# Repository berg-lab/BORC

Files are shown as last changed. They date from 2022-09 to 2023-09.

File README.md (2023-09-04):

# BORC
Battery-Operated Radiator Control

A low-power automatic radiator control that is designed to retrofit on steam radiators that use Honeywell's T104A1040 Zone Valve Operator
uses LowPowerLab's [DualOptiboot](https://github.com/LowPowerLab/DualOptiboot) bootloader for the ATmega1284P.

This repo contains:
- PCB design files and schematic for control board, power board and LED board for the BORC.
- Firmware for a low-power radiator control node
- Logger script to get real-time current data from the BORC

---

## Dependencies

To compile the firmware, [Arduino IDE 1.8.19](https://www.arduino.cc/en/software) or higher is required.

The firmware requires the following libraries installed:
- [RFM69](https://github.com/LowPowerLab/RFM69)
- [SPIFlash](https://github.com/LowPowerLab/SPIFlash)
- [LowPower](https://github.com/LowPowerLab/LowPower)
- [Adafruit PWM Servo Driver Library](https://github.com/adafruit/Adafruit-PWM-Servo-Driver-Library)

The firmware also requires the Moteino Board definitions installed following [this guide](https://lowpowerlab.com/guide/moteino/programming-libraries/).

---

## Logger script

The [logger script](https://github.com/berg-lab/BORC/blob/master/logger/logger.py) enables capturing current usage data over the serial port on the BORC.

### Prerequisites:
- [pip](https://pip.pypa.io/en/stable/installation/)
- [Pyserial](https://pypi.org/project/pyserial/)

### Run:
Run the script using the following command over a command line interface:

_For Windows:_
```
python logger.py -c COM15 -n filename
```

_For MacOS/Linux:_
```
python logger.py -c /dev/ttyusb0 -n filename
```

### Notes:
- Change `python` to `python3` if using Python version 3.
- Change `filename` to something referencing the test to keep the generated files organized. The current date/time is automatically added to the filename.
- The script automatically adds the `.csv` extension to the filename, so there's no need to include it in the arguments when running it.
- For Windows, go to device manager and find the COM port of the BORC under "Ports" section and replace `COM15` in the command above.
- For MacOS or Linux, use `ls /dev/tty.*` command in terminal to find the COM port of the BORC, and replace `/dev/ttyusb0` above with the full path of the COM port.
- Use `-h` command to bring a help menu (eg. `python logger.py -h`).
- If the servo doesn't move in some areas, you can adjust the default min and max limits to the particular servo installed. The default limits should be set to where the servo is guaranteed to move, and beyond these limits, the servo will not respond. Typical min limit for a 270° servo is 3600 and max limit is 3950. You can increase or decrease these limits to see where the servo being tested begins to move.
- Default baudrate for the BORC is `115200`. If updated, make sure to update the same in the logger script.

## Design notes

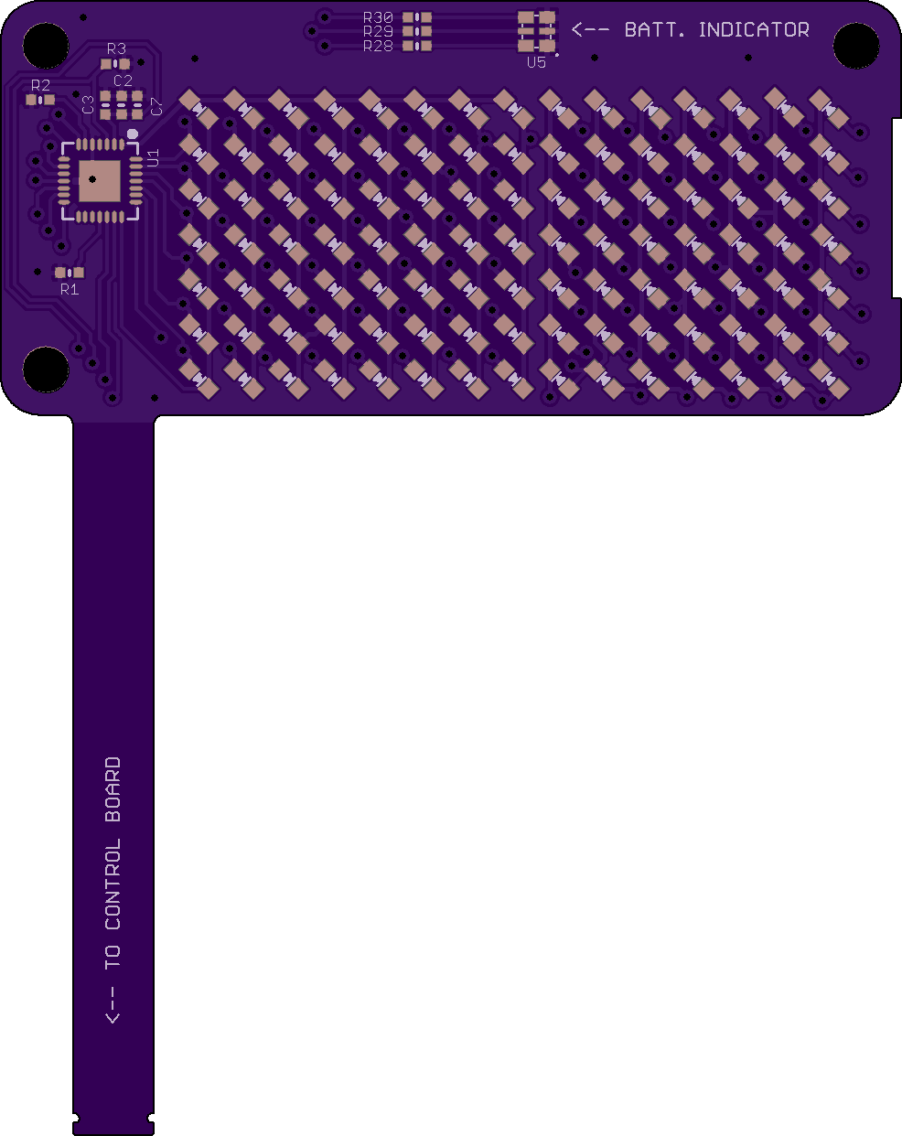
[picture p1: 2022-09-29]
hardware/LED_Board/top_render.png

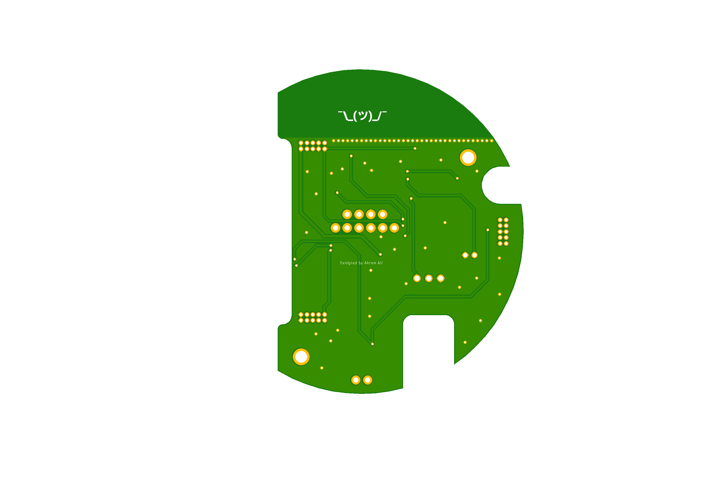
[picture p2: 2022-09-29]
hardware/power_board/bottom_render.png

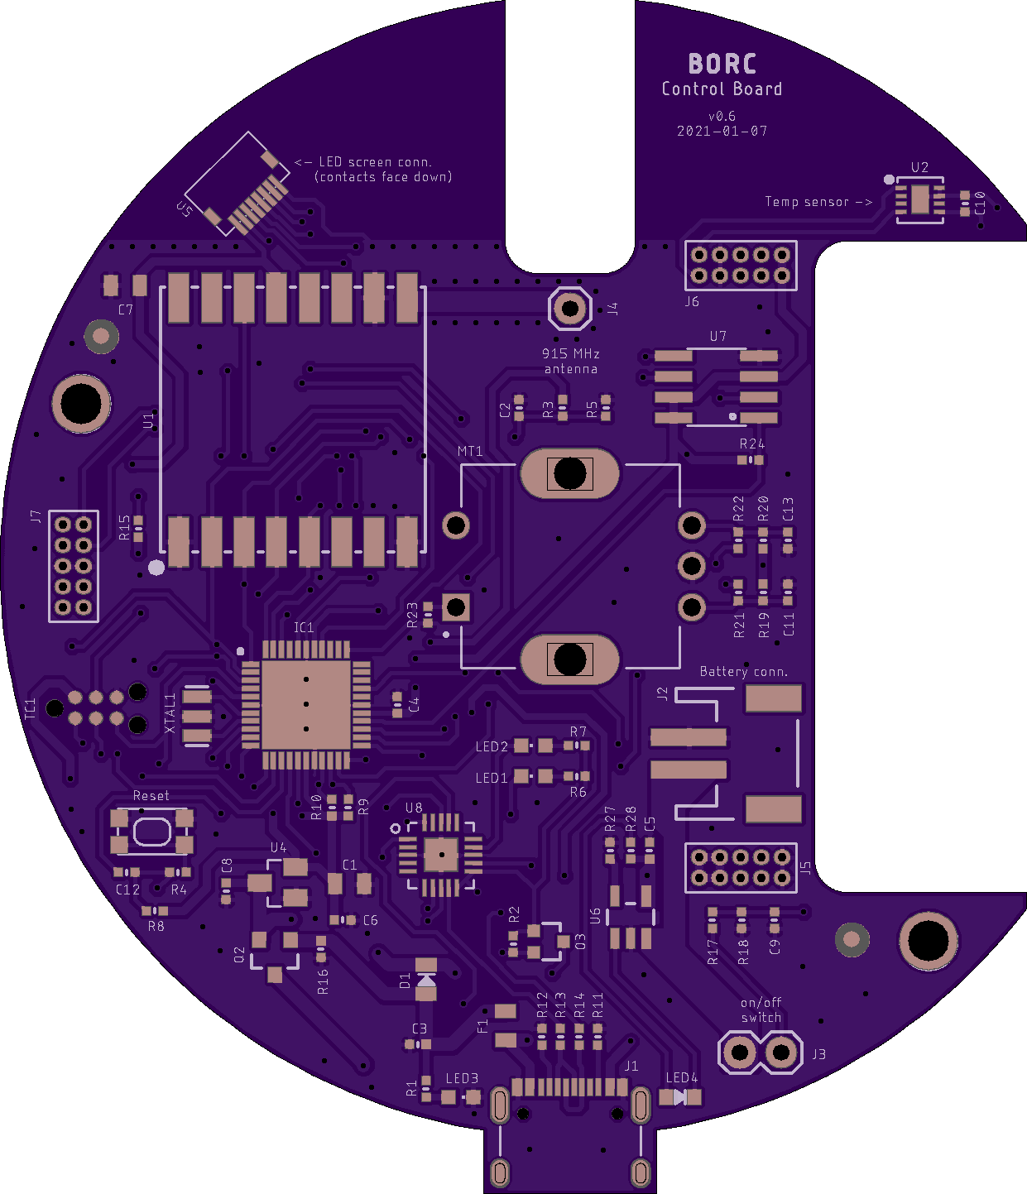
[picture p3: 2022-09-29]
hardware/control_board/top_render.png

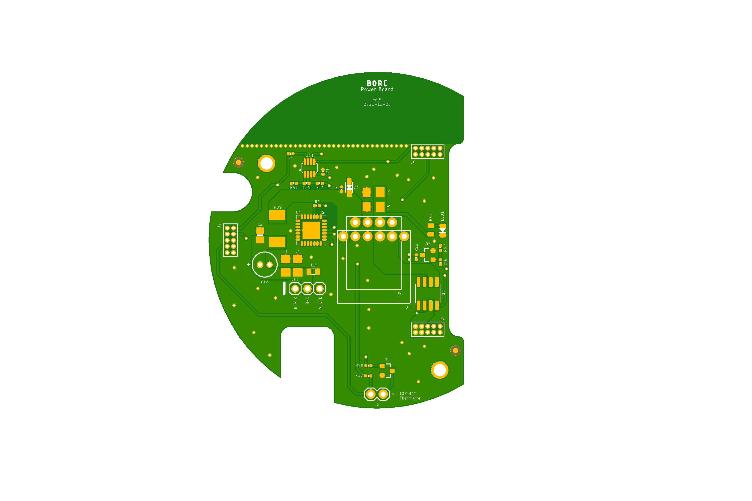
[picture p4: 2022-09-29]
hardware/power_board/top_render.png

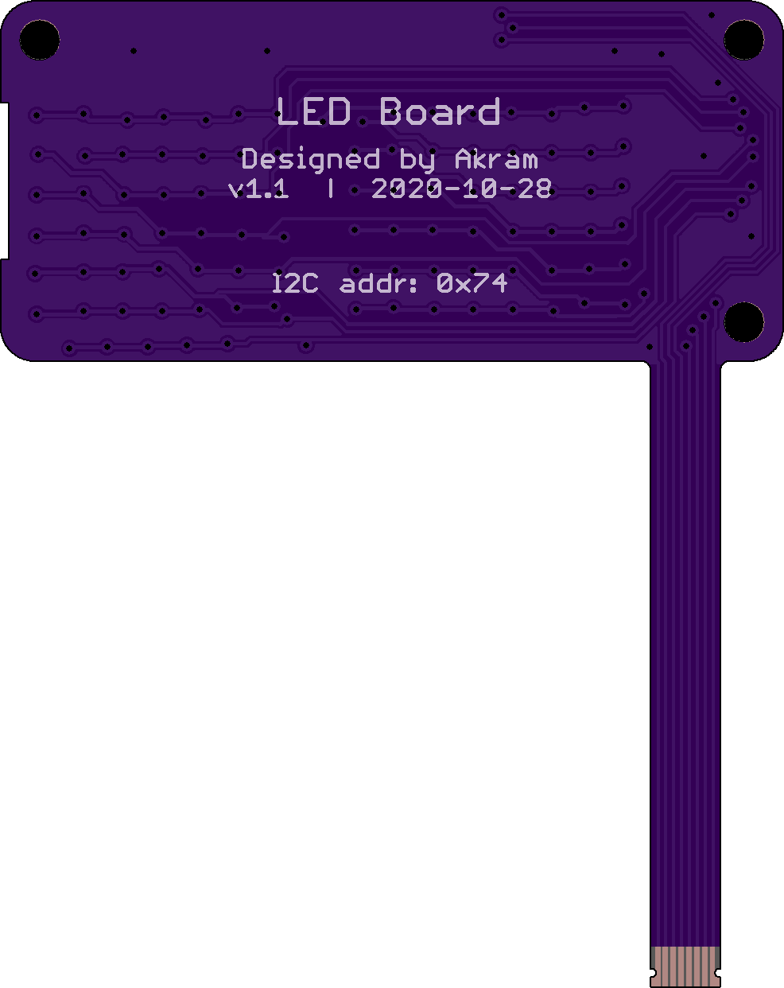
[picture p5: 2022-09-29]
hardware/LED_Board/bottom_render.png

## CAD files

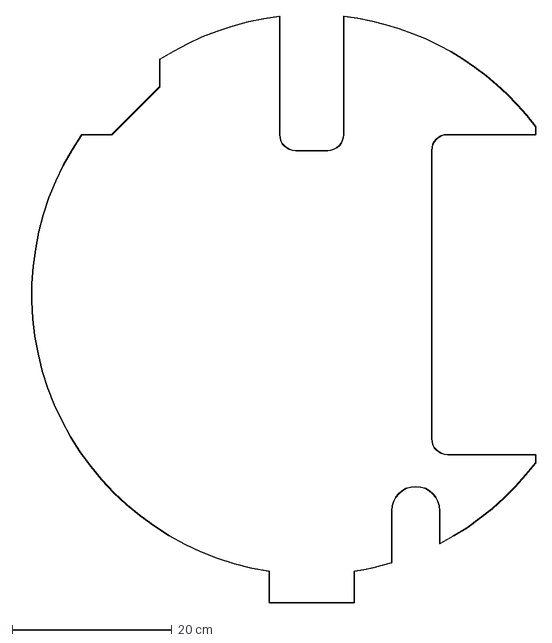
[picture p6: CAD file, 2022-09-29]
hardware/control_board/Control board outline v4.dxf
64.9 x 73.3 cm

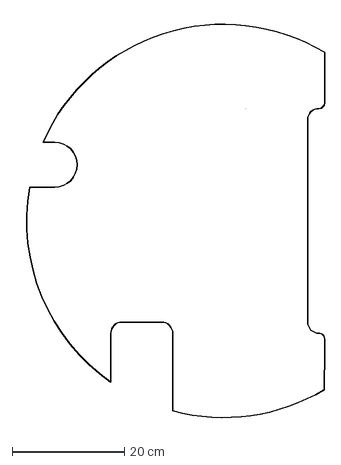
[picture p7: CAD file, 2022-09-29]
hardware/power_board/Power board PCB outline v0.3.dxf
54.8 x 72.7 cm

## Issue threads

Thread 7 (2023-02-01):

Fix BORC Melting Issue

amitche8, 2023-02-01:
Try different designs BORC Base to solve heating issues

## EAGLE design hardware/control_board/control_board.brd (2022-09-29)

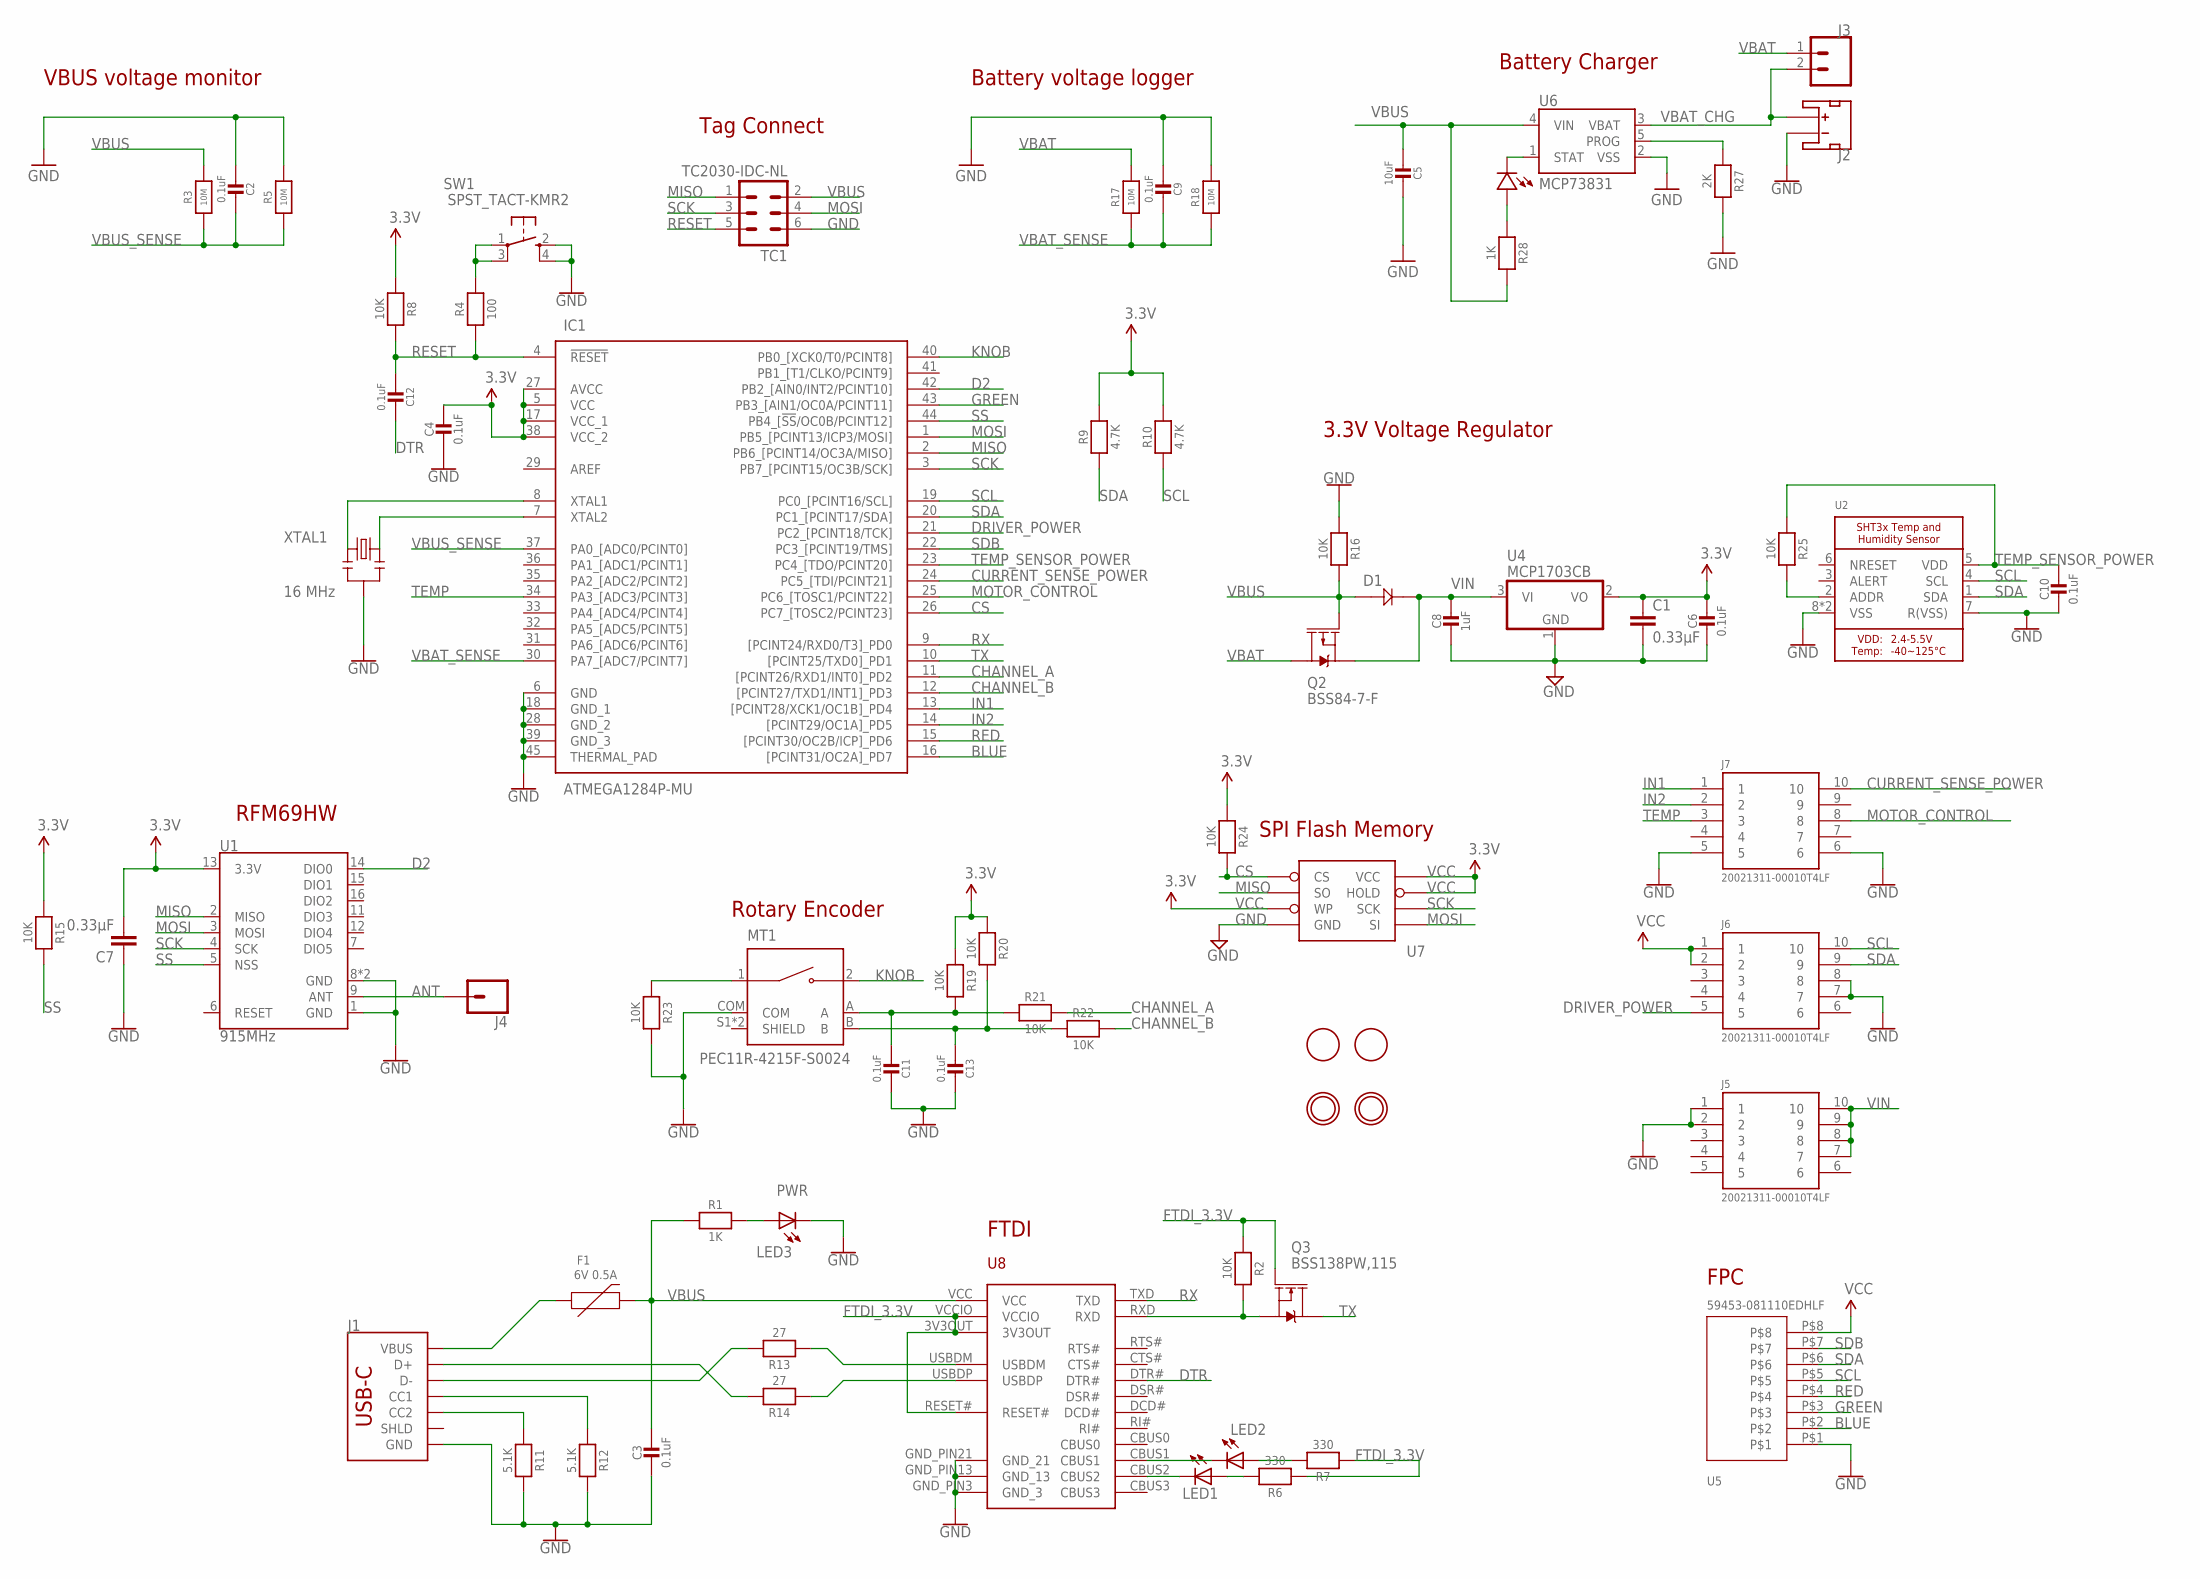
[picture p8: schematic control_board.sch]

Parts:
C1, C7: 0.33µF; 0805
C2, C3, C4, C6, C9, C10, C11, C12, C13: 0.1uF; MICROBUILDER__0402MP; MPN GRM155R71C104KA88J
C5: 10uF; MICROBUILDER__0402MP; MPN GRM155R71C104KA88J
C8: 1uF; MICROBUILDER__0402MP; MPN GRM155R71C104KA88J
D1: DIODE_SCHOTTKY0805-RES; 0805
F1: 6V 0.5A; 0805; MPN MF-PSML110-2
IC1: ATMEGA1284P-MU; QFN50P700X700X100-45N
J1: USB Female Type C Connector; USB-C-16P-2LAYER-PADS
J2: JST_2MM_MALE; JST-2-SMD
J3: CONN_02; 1X02
J4: CONN_01; 1X01
J5, J6, J7: 20021311-00010T4LF; HEADER_1.27MM_2X5
LED1, LED2: LEDCHIPLED_0603; CHIPLED_0603
LED3: PWR; CHIPLED_0603
LED4: LED0603; 0603-LED
MT1: PEC11R-4215F-S0024; XDCR_PEC11R-4215F-S0024
Q2: BSS84-7-F; SOT23-3
Q3: BSS138PW,115; SOT323
R1, R28: 1K; MICROBUILDER__0402MP; MPN RC0402FR-7W10KL
R2, R8, R15, R16, R19, R20, R21, R22, R23, R24, R25: 10K; MICROBUILDER__0402MP; MPN RC0402FR-7W10KL
R3, R5, R17, R18: 10M; MICROBUILDER__0402MP; MPN RC0402JR-0710KL
R4: 100; MICROBUILDER__0402MP; MPN RC0402FR-7W10KL
R6, R7: 330; MICROBUILDER__0402MP; MPN RC0402FR-7W10KL
R9, R10: 4.7K; MICROBUILDER__0402MP; MPN RC0402FR-7W10KL
R11, R12: 5.1K; MICROBUILDER__0402MP; MPN RC0402FR-7W10KL
R13, R14: 27; MICROBUILDER__0402MP; MPN RC0402FR-7W10KL
R27: 2K; MICROBUILDER__0402MP; MPN RC0402FR-7W10KL
SW1: SPST_TACT-KMR2; KMR2
TC1: TC2030-IDC-NL
U1: 915MHz; RFM69HCW-XXXS2
U2: SHT3X
U4: MCP1703CB; SOT23
U5: 59453-081110EDHLF
U6: MCP73831; SOT23-5
U7: AT25F512BJEDEC_3.9MM; SO08
U8: FT231XQ-R; FTDI_FT231XQ-R_PACKAGE
U$2, U$3: MOUNTINGHOLE2.5; MOUNTINGHOLE_2.5_PLATED
U$8, U$9: FIDUCIAL; FIDUCIAL_1MM
XTAL1: 16 MHz; RESONATOR-SMD

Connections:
A: C11.2, MT1.A, R19.2, R21.1
ANT: J4.1, U1.9 (ANT)
B: C13.2, MT1.B, R20.2, R22.1
BLUE: IC1.16 ([PCINT31/OC2A]_PD7), U5.P$2
CHANNEL_A: IC1.11 ([PCINT26/RXD1/INT0]_PD2), R21.2
CHANNEL_B: IC1.12 ([PCINT27/TXD1/INT1]_PD3), R22.2
CS: IC1.26 (PC7_[TOSC2/PCINT23]), R24.2, U7.1_CS (CS)
CURRENT_SENSE_POWER: IC1.24 (PC5_[TDI/PCINT21]), J7.10
D2: IC1.42 (PB2_[AIN0/INT2/PCINT10]), U1.14 (DIO0)
DRIVER_POWER: IC1.21 (PC2_[PCINT18/TCK]), J6.5
DTR: C12.1, U8.DTR#
FTDI_3.3V: Q3.1 (G), R2.1, R6.1, R7.1, U8.3V3OUT, U8.RESET#, U8.VCCIO
GND: C1.2, C2.2, C3.2, C4.2, C5.1, C6.2, C7.1, C8.2, C9.2, C10.2, C11.1, C13.1, IC1.6 (GND), IC1.18 (GND_1), IC1.28 (GND_2), IC1.39 (GND_3), IC1.45 (THERMAL_PAD), J1.GND, J1.GND2 (GND), J2.1 (-), J5.1, J5.2, J6.7, J6.8, J7.5, J7.6, LED3.C, MT1.COM, R5.2, R11.2, R12.2, R16.1, R18.2, R23.2, R27.2, SW1.2 (S), SW1.4 (S1), TC1.6, U1.1 (GND), U1.8 (GND), U1.10 (GND), U2.7 (R(VSS)), U2.8 (VSS), U2.THERMAL (VSS), U4.1 (GND), U5.P$1, U6.2 (VSS), U7.4_GND (GND), U8.GND_PIN3 (GND_3), U8.GND_PIN13 (GND_13), U8.GND_PIN21 (GND_21), XTAL1.2
GREEN: IC1.43 (PB3_[AIN1/OC0A/PCINT11]), U5.P$3
IN1: IC1.13 ([PCINT28/XCK1/OC1B]_PD4), J7.1
IN2: IC1.14 ([PCINT29/OC1A]_PD5), J7.2
KNOB: IC1.40 (PB0_[XCK0/T0/PCINT8]), MT1.2
MISO: IC1.2 (PB6_[PCINT14/OC3A/MISO]), TC1.1, U1.2 (MISO), U7.2_SO (SO)
MOSI: IC1.1 (PB5_[PCINT13/ICP3/MOSI]), TC1.4, U1.3 (MOSI), U7.5_SI (SI)
MOTOR_CONTROL: IC1.25 (PC6_[TOSC1/PCINT22]), J7.8
unnamed: IC1.8 (XTAL1), XTAL1.1
unnamed: LED3.A, R1.2
unnamed: IC1.7 (XTAL2), XTAL1.3
unnamed: J1.B5 (CC2), R11.1
unnamed: J1.A5 (CC1), R12.1
unnamed: J1.A6 (D+), J1.B6 (D+), R14.2
unnamed: J1.A7 (D-), J1.B7 (D-), R13.2
unnamed: R14.1, U8.USBDP
unnamed: R13.1, U8.USBDM
unnamed: F1.1, J1.VBUS1 (VBUS), J1.VBUS2 (VBUS)
unnamed: MT1.1, R23.1
unnamed: R4.2, SW1.1, SW1.3 (P1)
unnamed: LED1.C, U8.CBUS2
unnamed: Q3.2 (S), R2.2, U8.RXD
unnamed: LED1.A, R6.2
unnamed: LED4.PLUS, R28.1
unnamed: LED2.A, R7.2
unnamed: LED2.C, U8.CBUS1
unnamed: LED4.MINUS, U6.1 (STAT)
unnamed: R25.2, U2.2 (ADDR)
PROG1: R27.1, U6.5 (PROG)
RED: IC1.15 ([PCINT30/OC2B/ICP]_PD6), U5.P$4
RESET: C12.2, IC1.4 (!RESET), R4.1, R8.2, TC1.5
RX: IC1.9 ([PCINT24/RXD0/T3]_PD0), U8.TXD
SCK: IC1.3 (PB7_[PCINT15/OC3B/SCK]), TC1.3, U1.4 (SCK), U7.6_SCK (SCK)
SCL: IC1.19 (PC0_[PCINT16/SCL]), J6.10, R10.1, U2.4 (SCL), U5.P$5
SDA: IC1.20 (PC1_[PCINT17/SDA]), J6.9, R9.1, U2.1 (SDA), U5.P$6
SDB: IC1.22 (PC3_[PCINT19/TMS]), U5.P$7
SS: IC1.44 (PB4_[!SS!/OC0B/PCINT12]), R15.2, U1.5 (NSS)
TEMP: IC1.34 (PA3_[ADC3/PCINT3]), J7.3
TEMP_SENSOR_POWER: C10.1, IC1.23 (PC4_[TDO/PCINT20]), R25.1, U2.5 (VDD)
TX: IC1.10 ([PCINT25/TXD0]_PD1), Q3.3 (D)
VBAT: J3.1, Q2.3 (D1), R17.2
VBAT_CHG: J2.2 (+), J3.2, U6.3 (VBAT)
VBAT_SENSE: C9.1, IC1.30 (PA7_[ADC7/PCINT7]), R17.1, R18.1
VBUS: C3.1, C5.2, D1.1, F1.2, Q2.1 (G1), R1.1, R3.2, R16.2, R28.2, TC1.2, U6.4 (VIN), U8.VCC
VBUS_SENSE: C2.1, IC1.37 (PA0_[ADC0/PCINT0]), R3.1, R5.1
VCC: C1.1, C4.1, C6.1, C7.2, IC1.5 (VCC), IC1.17 (VCC_1), IC1.27 (AVCC), IC1.38 (VCC_2), J6.1, J6.2, R8.1, R9.2, R10.2, R15.1, R19.1, R20.1, R24.1, U1.13 (3.3V), U4.2 (VO), U5.P$8, U7.3_WP (WP), U7.7_HOLD (HOLD), U7.8_VCC (VCC)
VIN: C8.1, D1.2, J5.7, J5.8, J5.9, J5.10, Q2.2 (S1), U4.3 (VI)

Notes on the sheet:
Battery Charger
Battery voltage logger
3.3V Voltage Regulator
SPI Flash Memory
Rotary Encoder
Tag Connect
RFM69HW
FTDI
FPC
VBUS voltage monitor

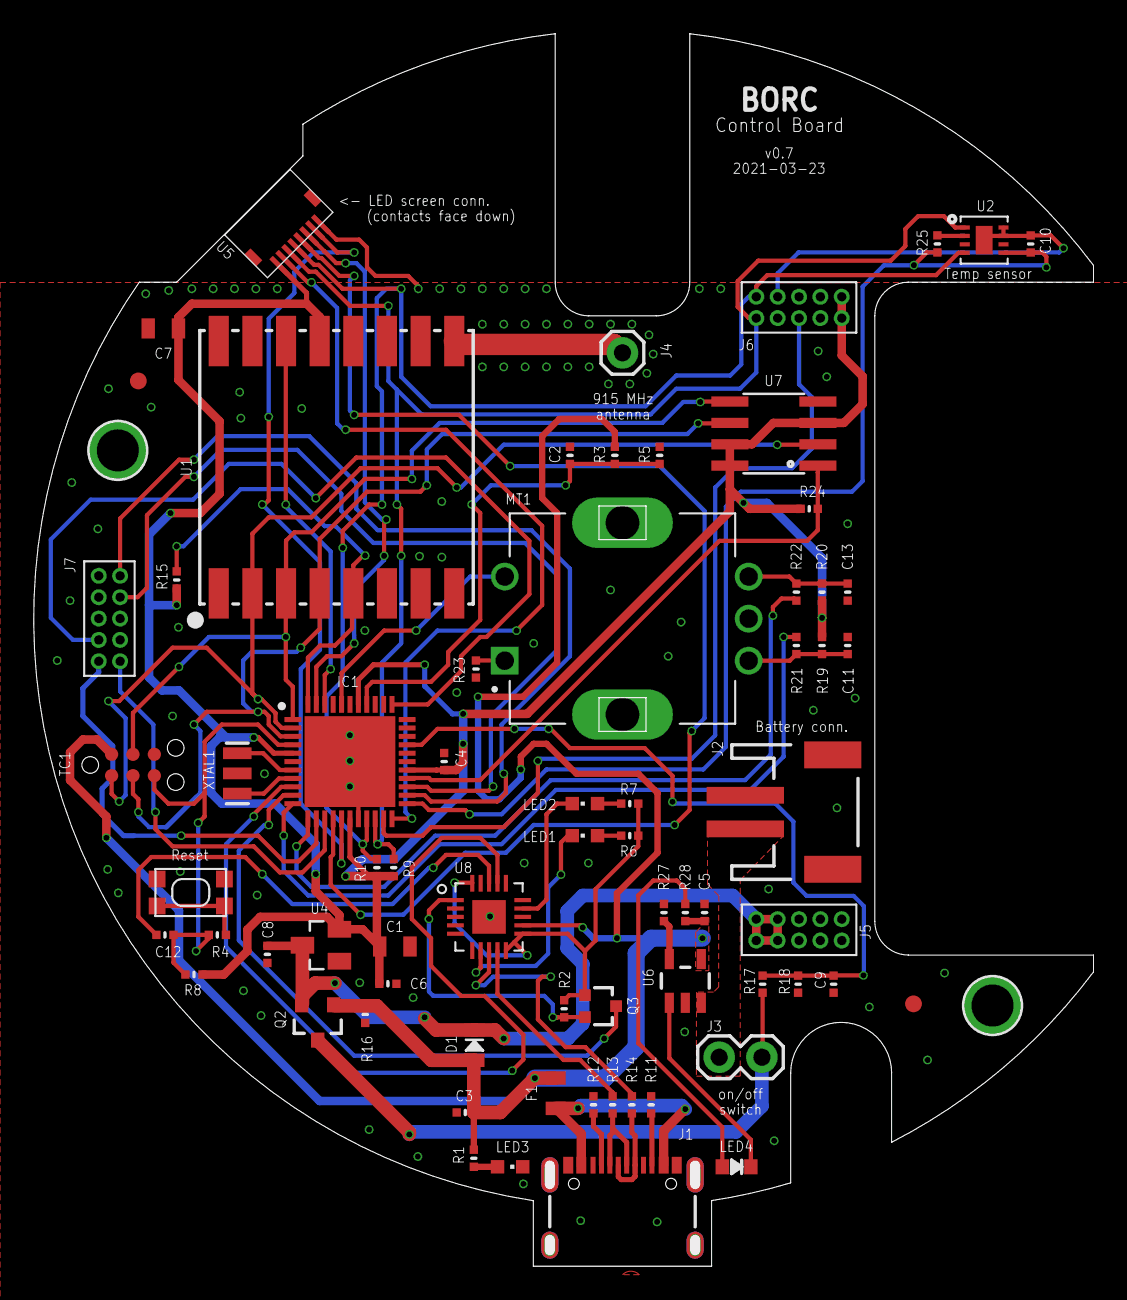
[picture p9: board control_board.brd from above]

Board: 2 copper layers, 63.0 x 73.3 mm, 71 parts (0 on the bottom side), 59 nets.

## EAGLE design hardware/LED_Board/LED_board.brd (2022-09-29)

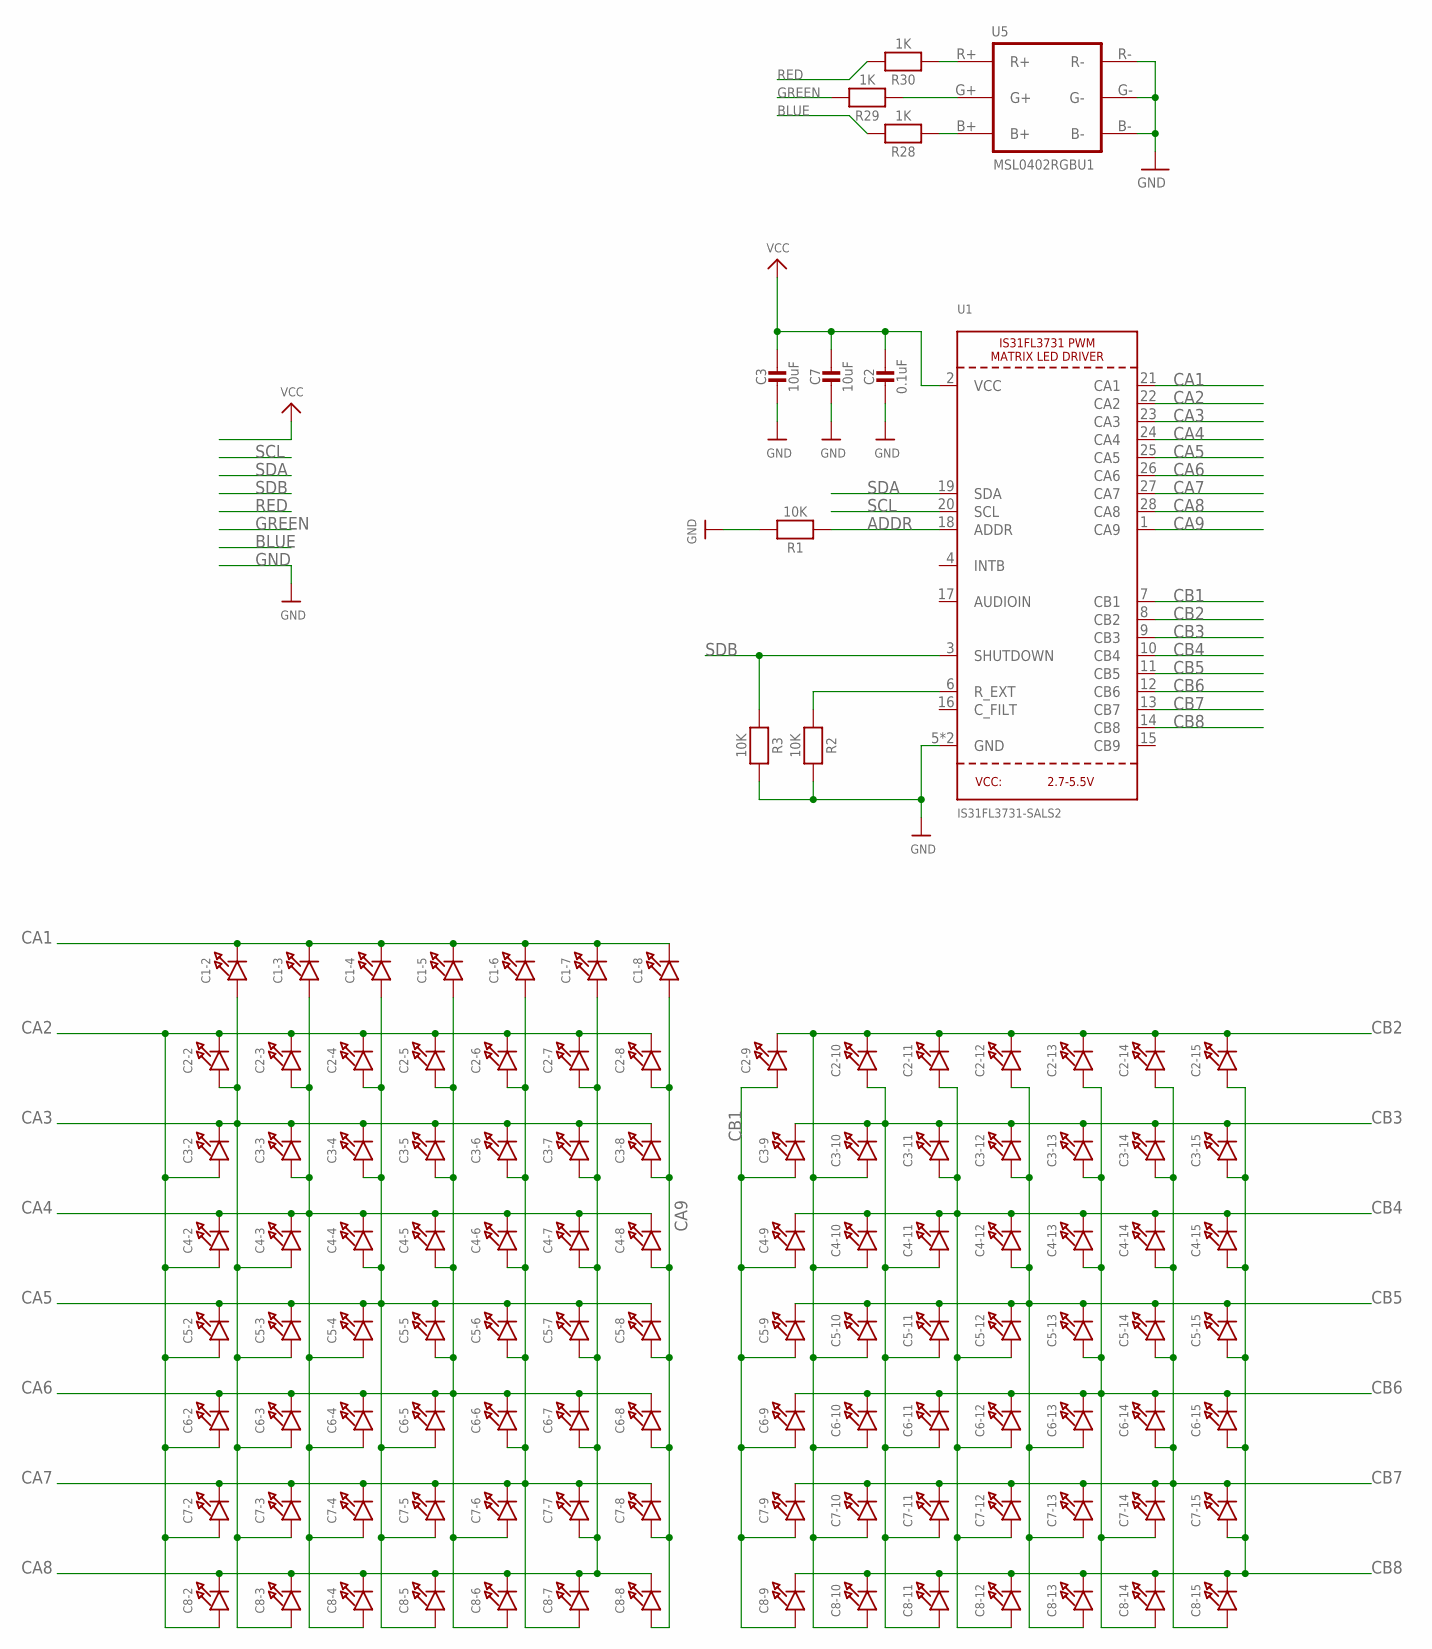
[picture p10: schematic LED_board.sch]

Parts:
C1-2, C1-3, C1-4, C1-5, C1-6, C1-7, C1-8, C2-2, C2-3, C2-4, C2-5, C2-6, C2-7, C2-8, C2-9, C2-10, C2-11, C2-12, C2-13, C2-14, C2-15, C3-2, C3-3, C3-4, C3-5, C3-6, C3-7, C3-8, C3-9, C3-10, C3-11, C3-12, C3-13, C3-14, C3-15, C4-2, C4-3, C4-4, C4-5, C4-6, C4-7, C4-8, C4-9, C4-10, C4-11, C4-12, C4-13, C4-14, C4-15, C5-2, C5-3, C5-4, C5-5, C5-6, C5-7, C5-8, C5-9, C5-10, C5-11, C5-12, C5-13, C5-14, C5-15, C6-2, C6-3, C6-4, C6-5, C6-6, C6-7, C6-8, C6-9, C6-10, C6-11, C6-12, C6-13, C6-14, C6-15, C7-2, C7-3, C7-4, C7-5, C7-6, C7-7, C7-8, C7-9, C7-10, C7-11, C7-12, C7-13, C7-14, C7-15, C8-2, C8-3, C8-4, C8-5, C8-6, C8-7, C8-8, C8-9, C8-10, C8-11, C8-12, C8-13, C8-14, C8-15: LED0603_NOOUTLINE; CHIPLED_0603_NOOUTLINE
C2: 0.1uF; MICROBUILDER__0402MP; MPN GRM155R71C104KA88J
C3, C7: 10uF; MICROBUILDER__0402MP; MPN GRM155R71C104KA88J
R1, R2, R3: 10K; MICROBUILDER__0402MP; MPN RC0402FR-7W10KL
R28, R29, R30: 1K; MICROBUILDER__0402MP; MPN RC0402FR-7W10KL
U1: IS31FL3731-SALS2; QFN28_4MM_0.4MM
U5: MSL0402RGBU1; SMD-6; MPN MSL0402RGBU1

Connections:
ADDR: R1.1, U1.18 (ADDR)
BLUE: R28.2
CA1: C1-2.C, C1-3.C, C1-4.C, C1-5.C, C1-6.C, C1-7.C, C1-8.C, U1.21 (CA1)
CA2: C2-2.C, C2-3.C, C2-4.C, C2-5.C, C2-6.C, C2-7.C, C2-8.C, C3-2.A, C4-2.A, C5-2.A, C6-2.A, C7-2.A, C8-2.A, U1.22 (CA2)
CA3: C1-2.A, C2-2.A, C3-2.C, C3-3.C, C3-4.C, C3-5.C, C3-6.C, C3-7.C, C3-8.C, C4-3.A, C5-3.A, C6-3.A, C7-3.A, C8-3.A, U1.23 (CA3)
CA4: C1-3.A, C2-3.A, C3-3.A, C4-2.C, C4-3.C, C4-4.C, C4-5.C, C4-6.C, C4-7.C, C4-8.C, C5-4.A, C6-4.A, C7-4.A, C8-4.A, U1.24 (CA4)
CA5: C1-4.A, C2-4.A, C3-4.A, C4-4.A, C5-2.C, C5-3.C, C5-4.C, C5-5.C, C5-6.C, C5-7.C, C5-8.C, C6-5.A, C7-5.A, C8-5.A, U1.25 (CA5)
CA6: C1-5.A, C2-5.A, C3-5.A, C4-5.A, C5-5.A, C6-2.C, C6-3.C, C6-4.C, C6-5.C, C6-6.C, C6-7.C, C6-8.C, C7-6.A, C8-6.A, U1.26 (CA6)
CA7: C1-6.A, C2-6.A, C3-6.A, C4-6.A, C5-6.A, C6-6.A, C7-2.C, C7-3.C, C7-4.C, C7-5.C, C7-6.C, C7-7.C, C7-8.C, C8-7.A, U1.27 (CA7)
CA8: C1-7.A, C2-7.A, C3-7.A, C4-7.A, C5-7.A, C6-7.A, C7-7.A, C8-2.C, C8-3.C, C8-4.C, C8-5.C, C8-6.C, C8-7.C, C8-8.C, U1.28 (CA8)
CA9: C1-8.A, C2-8.A, C3-8.A, C4-8.A, C5-8.A, C6-8.A, C7-8.A, C8-8.A, U1.1 (CA9)
CB1: C2-9.A, C3-9.A, C4-9.A, C5-9.A, C6-9.A, C7-9.A, C8-9.A, U1.7 (CB1)
CB2: C2-9.C, C2-10.C, C2-11.C, C2-12.C, C2-13.C, C2-14.C, C2-15.C, C3-10.A, C4-10.A, C5-10.A, C6-10.A, C7-10.A, C8-10.A, U1.8 (CB2)
CB3: C2-10.A, C3-9.C, C3-10.C, C3-11.C, C3-12.C, C3-13.C, C3-14.C, C3-15.C, C4-11.A, C5-11.A, C6-11.A, C7-11.A, C8-11.A, U1.9 (CB3)
CB4: C2-11.A, C3-11.A, C4-9.C, C4-10.C, C4-11.C, C4-12.C, C4-13.C, C4-14.C, C4-15.C, C5-12.A, C6-12.A, C7-12.A, C8-12.A, U1.10 (CB4)
CB5: C2-12.A, C3-12.A, C4-12.A, C5-9.C, C5-10.C, C5-11.C, C5-12.C, C5-13.C, C5-14.C, C5-15.C, C6-13.A, C7-13.A, C8-13.A, U1.11 (CB5)
CB6: C2-13.A, C3-13.A, C4-13.A, C5-13.A, C6-9.C, C6-10.C, C6-11.C, C6-12.C, C6-13.C, C6-14.C, C6-15.C, C7-14.A, C8-14.A, U1.12 (CB6)
CB7: C2-14.A, C3-14.A, C4-14.A, C5-14.A, C6-14.A, C7-9.C, C7-10.C, C7-11.C, C7-12.C, C7-13.C, C7-14.C, C7-15.C, C8-15.A, U1.13 (CB7)
CB8: C2-15.A, C3-15.A, C4-15.A, C5-15.A, C6-15.A, C7-15.A, C8-9.C, C8-10.C, C8-11.C, C8-12.C, C8-13.C, C8-14.C, C8-15.C, U1.14 (CB8)
GND: C2.2, C3.2, C7.2, R1.2, R2.2, R3.2, U1.5 (GND), U1.THERMAL (GND), U5.B-, U5.G-, U5.R-
GREEN: R29.2
unnamed: R28.1, U5.B+
unnamed: R30.1, U5.R+
unnamed: R29.1, U5.G+
RED: R30.2
R_EXT: R2.1, U1.6 (R_EXT)
SCL: U1.20 (SCL)
SDA: U1.19 (SDA)
SDB: R3.1, U1.3 (SHUTDOWN)
VCC: C2.1, C3.1, C7.1, U1.2 (VCC)

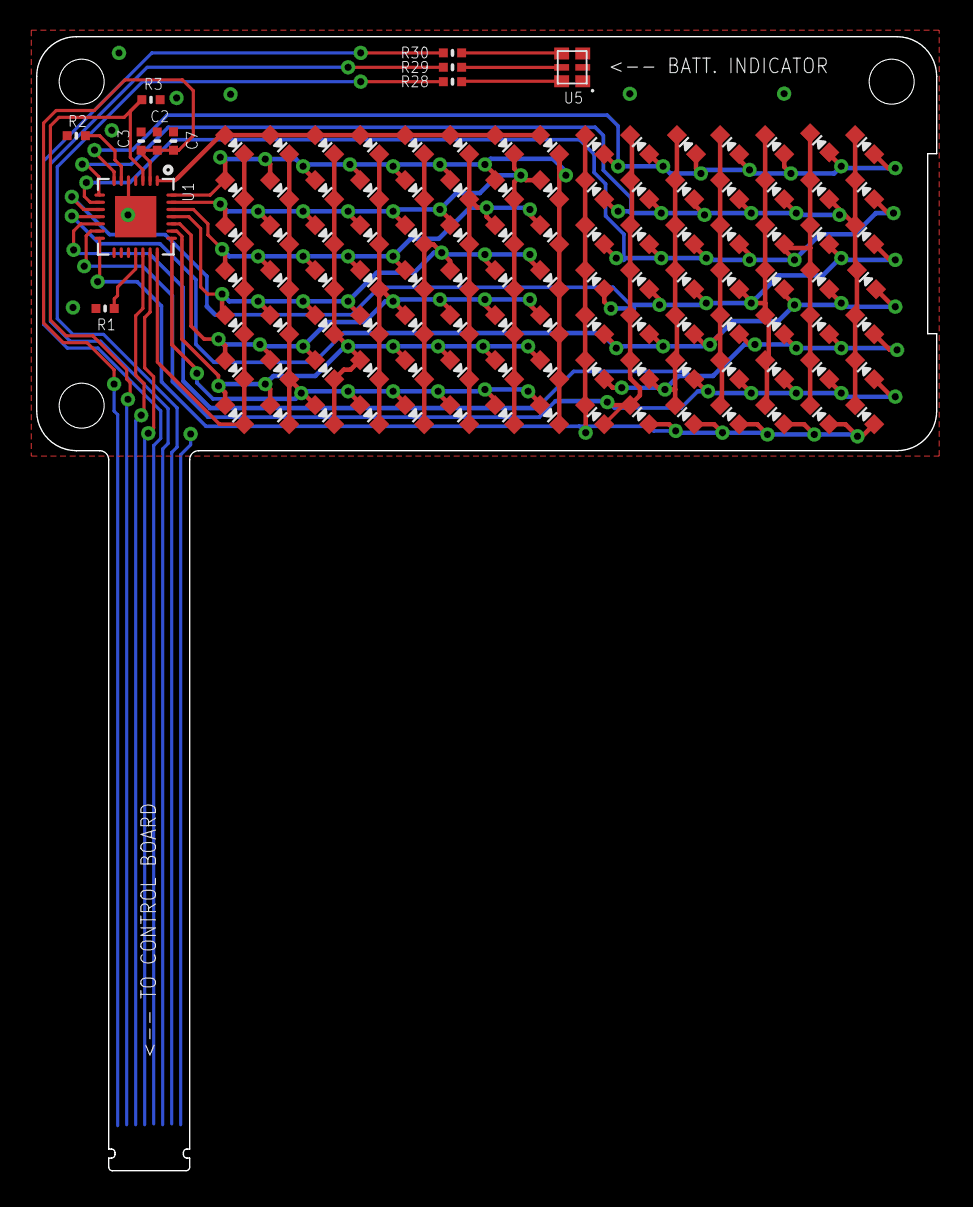
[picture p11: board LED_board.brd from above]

Board: 2 copper layers, 50.0 x 63.0 mm, 116 parts (0 on the bottom side), 25 nets.

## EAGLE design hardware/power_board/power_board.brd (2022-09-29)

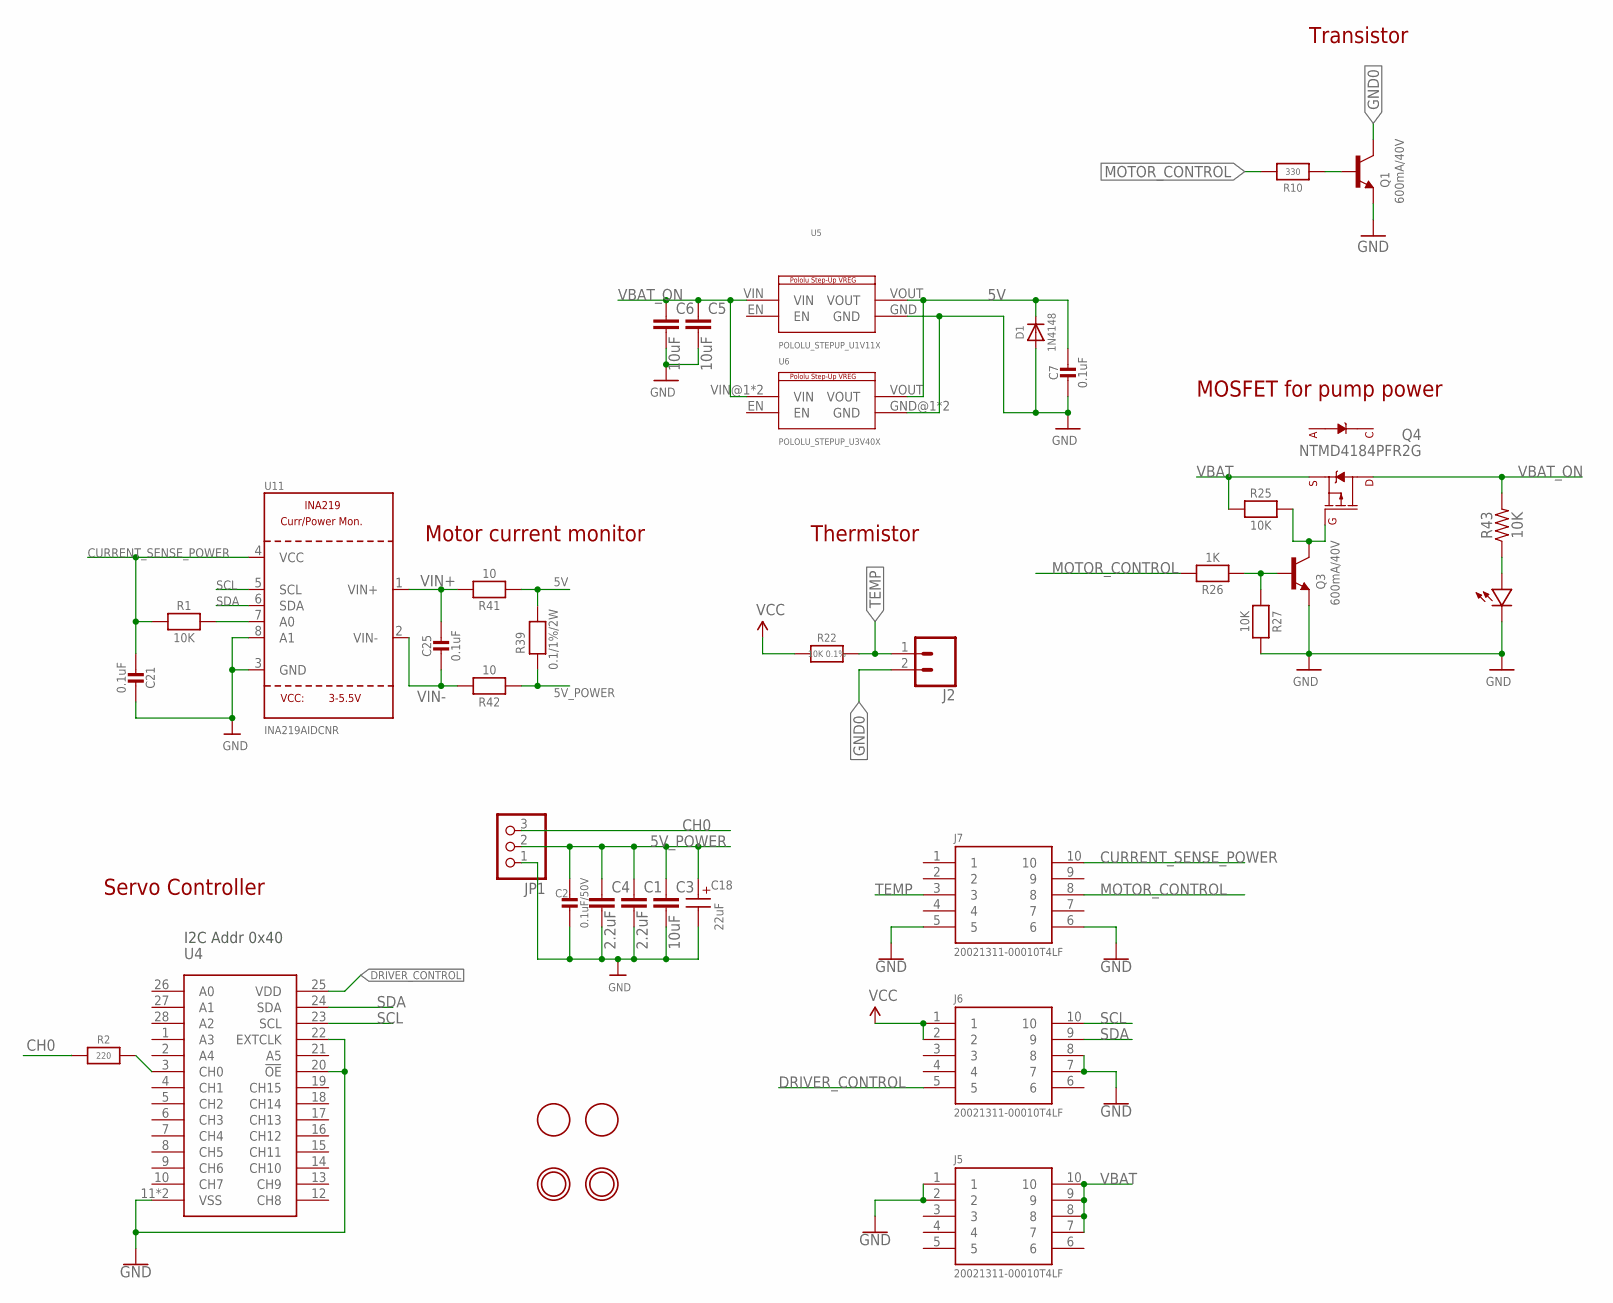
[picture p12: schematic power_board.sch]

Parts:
C1, C4: 2.2uF; 1206
C2: 0.1uF/50V; 0805-NO
C3: 10uF; 0805
C5, C6: 10uF; 1206
C7, C21, C25: 0.1uF; MICROBUILDER__0402MP; MPN GRM155R71C104KA88J
C18: 22uF; WCAP-ATLL_5X11(DXL); MPN 860160672011
D1: 1N4148; SOD-323; MPN 1N4148WX-TP
J2: CONN_02; 1X02
J5, J6, J7: 20021311-00010T4LF; HEADER_1.27MM_2X5
JP1: PINHD-1X3; 1X03
LED1: BLUE; 0805-LED; MPN 150080BS75000
Q1, Q3: 600mA/40V; SOT23-3; MPN MMBT3904-TP
Q4: NTMD4184PFR2G; SOIC-8; MPN NTMD4184PFR2G
R1, R25, R27: 10K; MICROBUILDER__0402MP; MPN RC0402FR-7W10KL
R2: 220; MICROBUILDER__0402MP; MPN RC0402JR-071KL
R10: 330; MICROBUILDER__0402MP; MPN RC0402JR-0710KL
R22: 10K 0.1%; MICROBUILDER__0402MP; MPN RC0402JR-0727RL
R26: 1K; MICROBUILDER__0402MP; MPN RC0402FR-101KL
R39: 0.1/1%/2W; 2512; MPN RCWE2512R100FKEA
R41, R42: 10; MICROBUILDER__0402MP; MPN RC0402FR-0710RL
R43: 10K; 0805; MPN RK73B2ATTD103J
U4: PCA9685HVQFN28; HVQFN28_SOT788-1
U5: POLOLU_STEPUP_U1V11X
U6: POLOLU_STEPUP_U3V40X
U11: INA219AIDCNR; SOT23-8; MPN INA219AIDCNR
U$2, U$3: MOUNTINGHOLE2.5; MOUNTINGHOLE_2.5_PLATED
U$8, U$9: FIDUCIAL; FIDUCIAL_1MM

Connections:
5V: C7.1, D1.C, R39.2, R41.1, U5.VOUT, U6.VOUT
5V_POWER: C1.1, C2.1, C3.1, C4.1, C18.1 (+), JP1.2, R39.1, R42.1
CH0: JP1.3, R2.1
CURRENT_SENSE_POWER: C21.2, J7.10, R1.1, U11.4 (VCC)
DRIVER_CONTROL: J6.5, U4.25 (VDD)
GND: C1.2, C2.2, C3.2, C4.2, C5.2, C6.2, C7.2, C18.2 (-), C21.1, D1.A, J5.1, J5.2, J6.7, J6.8, J7.5, J7.6, JP1.1, LED1.MINUS, Q1.2 (E), Q3.2 (E), R27.2, U4.11 (VSS), U4.20 (!OE), U4.22 (EXTCLK), U4.TH (VSS), U5.GND, U6.GND@1 (GND), U6.GND@2 (GND), U11.3 (GND), U11.8 (A1)
GND0: J2.2, Q1.3 (C)
MOTOR_CONTROL: J7.8, R10.2, R26.2
unnamed: R1.2, U11.7 (A0)
unnamed: Q1.1 (B), R10.1
unnamed: R2.2, U4.3 (CH0)
unnamed: LED1.PLUS, R43.1
unnamed: Q3.3 (C), Q4.4 (G), R25.2
unnamed: Q3.1 (B), R26.1, R27.1
SCL: J6.10, U4.23 (SCL), U11.5 (SCL)
SDA: J6.9, U4.24 (SDA), U11.6 (SDA)
TEMP: J2.1, J7.3, R22.2
VBAT: J5.7, J5.8, J5.9, J5.10, Q4.3 (S), R25.1
VBAT_ON: C5.1, C6.1, Q4.5 (D), Q4.6 (D), R43.2, U5.VIN, U6.VIN@1 (VIN), U6.VIN@2 (VIN)
VCC: J6.1, J6.2, R22.1
VIN+: C25.1, R41.2, U11.1 (VIN+)
VIN-: C25.2, R42.2, U11.2 (VIN-)

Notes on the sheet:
MOSFET for pump power
Motor current monitor
Thermistor
Transistor
I2C Addr 0x40
Servo Controller

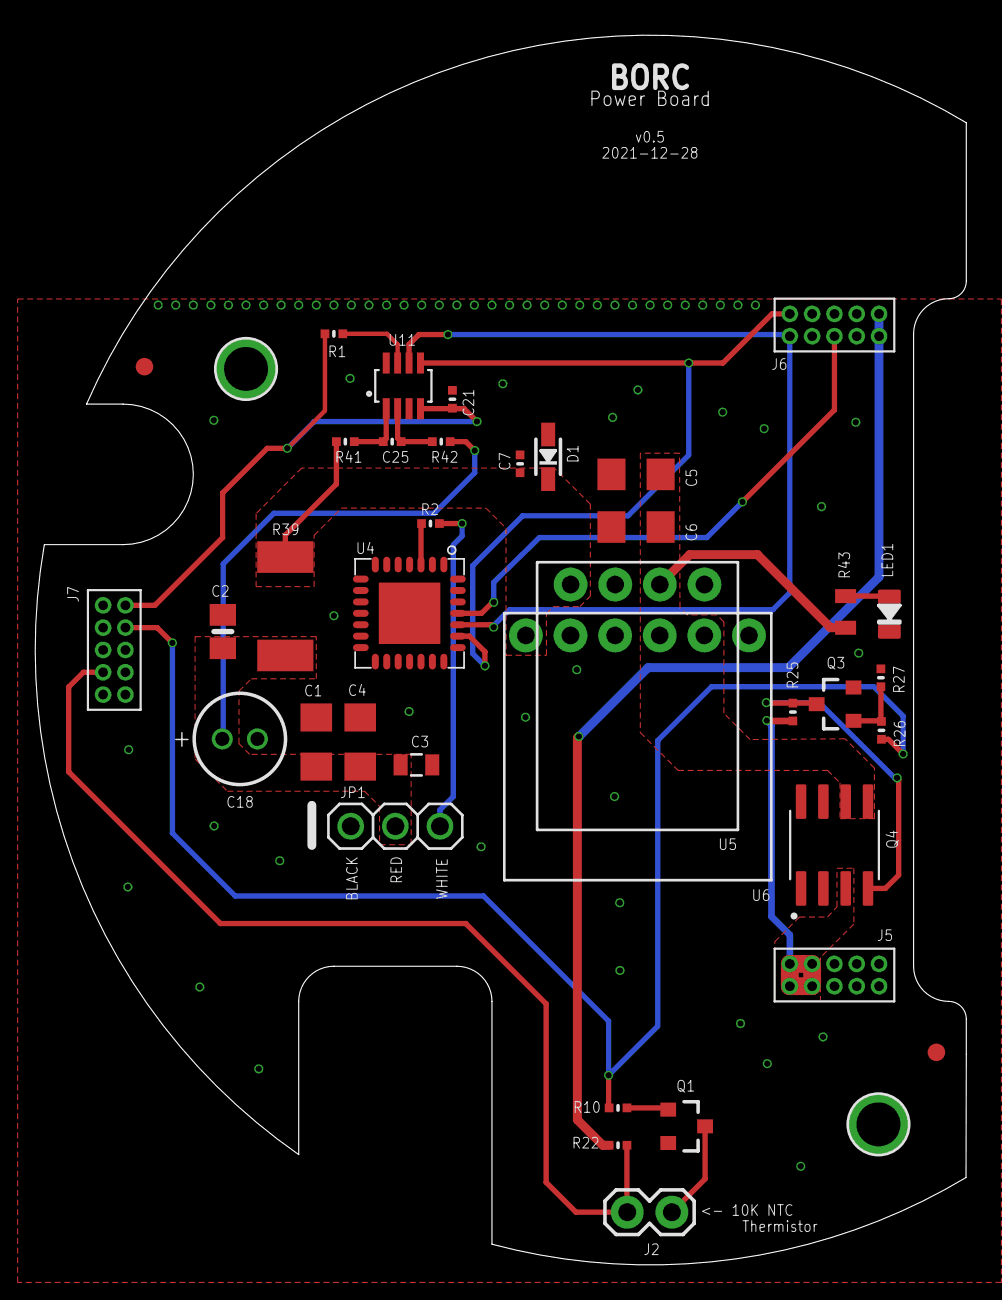
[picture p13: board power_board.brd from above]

Board: 2 copper layers, 53.0 x 70.0 mm, 39 parts (0 on the bottom side), 22 nets.

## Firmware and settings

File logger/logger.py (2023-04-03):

# -*- coding: utf-8 -*-

# This script sends commands to the BORC and reads back incoming serial data.
# All data is saved in individual csv files for post-processing.

#=========================================================================================================
# Import necessary modules
#=========================================================================================================
from datetime import datetime
import time
import serial
import getopt
import sys
import csv
#=========================================================================================================


#=========================================================================================================
# Global variables
#=========================================================================================================
DEFAULT_MIN_LIMIT = 3595
DEFAULT_MAX_LIMIT = 3930
servo_range = DEFAULT_MAX_LIMIT - DEFAULT_MIN_LIMIT
notches = 6
BAUDRATE = 115200
file_extention = ".csv"
header = ['Time', 'CURRENT', 'mA']
buffer = []
#=========================================================================================================


#=========================================================================================================
# Read arguments from cli and return them as a list
#=========================================================================================================
def read_args():

    global COM_port
    global filename

    # 1st argument is always script name, so remove it from the argument list
    argumentList = sys.argv[1:]
    
    # Options
    options = "hc:n:"
    
    # Long options
    long_options = ["Help", "COM Port = ", "File Name ="]
    
    try:
        # Parsing arguments
        arguments, values = getopt.getopt(argumentList, options, long_options)
        
        # check each argument
        for argument, value in arguments:
            
            # help/description
            if argument in ("-h"):
                print ("Use script like this: logger.py -c <COM Port> -n <filename>")
                sys.exit(1)
            
            # COM port
            elif argument in ("-c"):
                COM_port = value
            
            # file name
            elif argument in ("-n"):
                filename = timestamp + value   
    
    except getopt.error as err:
        # output error, and return with an error code
        print (str(err))
#=========================================================================================================


#=========================================================================================================
# move servo 
#=========================================================================================================
def move_servo(direction):

    # move servo from low to high
    if (direction == 0):
        send_serial_data('servo %d' % DEFAULT_MAX_LIMIT)
        save_data('0-6')

    # move servo from high to low
    elif (direction == 1):
        send_serial_data('servo %d' % DEFAULT_MIN_LIMIT)
        save_data('6-0')     

    # make servo move from one end to the other in increments
    else:
        
        for index in range(notches):

            # compute the next pwm value
            if (direction == 2):
                pwm_value = index * servo_range / notches + DEFAULT_MIN_LIMIT
                fn = str(index) + '-' + str(index+1)

            elif (direction == 3):
                pwm_value = DEFAULT_MAX_LIMIT - index * servo_range / notches
                fn = str(notches-index) + '-' + str(notches-index-1)

            # send command over serial
            send_serial_data('servo %d' % int(pwm_value))

            # get and save serial data
            save_data(fn)
            
            # wait a sec before moving to next position
            time.sleep(1)
#=========================================================================================================


#=========================================================================================================
# send data over serial
#=========================================================================================================
def send_serial_data(command):

    global buffer

    # add trailing newline and return to command
    command = str(command) + '\r\n'
    
    # send command over serial encoded in bytes format
    serialport.write(command.encode('utf-8'))

    # clear buffer list
    buffer = []

    # loop forever
    while True:

        # read data buffer line by line into a list
        data = serialport.readline().decode('utf-8').strip()

        # if we see a data line,  
        if (data.startswith('$:')):

            # remove spaces, remove leading marker, create a list separated by commas
            data = data.replace(' ', '').replace('$:,','').split(',')

            # and append to the main buffer list
            buffer.append(data)
            # print (data)

        # check for end marker
        elif (data.startswith('$$>>')):
            # end of data stream
            if (data == '$$>> OK' or data == '$$>> FAIL SYNTAX'):
                break
            else:
                datapoint = data.split()[2]
                print ('Room Temp: ' + str(datapoint) + ' ' + u'\N{DEGREE SIGN}' + 'F')
                break

#=========================================================================================================


#=========================================================================================================
# save data to file
#=========================================================================================================
def save_data(fn):

    global buffer
    global filename

    file_name = filename + '_' + fn + file_extention
    
    print (("Writing data to file: %s") % file_name)

    # open file in write mode and write 
    with open(file_name, 'w', newline='') as csvfile:
        csvwriter = csv.writer(csvfile)
        csvwriter.writerow(header)
        csvwriter.writerows(buffer)

    # close file
    csvfile.close()
#=========================================================================================================


#=========================================================================================================
# Main routine
#=========================================================================================================

print ('----- Servo current draw logger -----')

# get current datetime
timestamp = datetime.now().strftime('%Y-%m-%d_%H%M%S_')

# Read arguments from cli
read_args()

# try to initialize the serial port
try:
    serialport = serial.Serial(port=COM_port, baudrate=BAUDRATE, timeout=2) # make sure baud rate is the same

# if it didn't work, throw an exception
except:
    print('Opening serial port failed.')
    sys.exit(1)

# give some delay until serial port is properly opened
time.sleep(5)

# get temperature
send_serial_data('temp')
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

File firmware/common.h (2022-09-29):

#ifndef _COMMON_H_
#define _COMMON_H_
#include <stdint.h>


// Set to 1 for compiling on systems with very limited hardware
#define NO_HW 0

// system mode
enum mode_t : uint8_t
{
    MANUAL_MODE   = 0,
    MENU_MODE     = 1,
    SETPOINT_MODE = 2
};

// servo calibration mode
enum servocal_t : uint8_t
{
    NOTCAL = 0,
    CAL = 1,
    DONTCAL = 2
};

// radio packet type
enum packet_type_t  : uint8_t
{
    CONFIG_PACKET       = 0,
    TELEMETRY_PACKET    = 1,
    RESPONSE_PACKET     = 2
};

// Number of seconds that define a hardware-sleep period (base time = 32 secs)
#define SLEEP_TIME_SECS 32

// Misc. global variables ------------------------------------------
#define SERIAL_BAUD               115200

// I2C Addresses ---------------------------------------------------

#if NO_HW
  #define CURRENT_SENSE_ADDRESS   0x40
  #define TEMP_SENSE_ADDRESS      0x44
  #define SERVO_DRIVER_ADDRESS    0x00
  #define LED_MATRIX_ADDRESS      0x74
#else
  #define CURRENT_SENSE_ADDRESS   0x41  
  #define TEMP_SENSE_ADDRESS      0x45  
  #define SERVO_DRIVER_ADDRESS    0x40
  #define LED_MATRIX_ADDRESS      0x74
#endif



// Pin mapping -----------------------------------------------------
#define CLICK_PIN                 0
#define GREEN_PIN                 3
#define CHANNEL_B                 10
#define CHANNEL_A                 11
#define RED_PIN                   14
#define BLUE_PIN                  15
#define DRIVER_POWER_PIN          18
#define LED_SCREEN_POWER_PIN      19
#define TEMP_SENSOR_POWER_PIN     20
#define CURRENT_SENSE_POWER_PIN   21
#define SERVO_POWER_PIN           22
#define FLASH_SS                  23
#define VBUS_SENSE                A0
#define TEMP_SENSE                A3
#define VBAT_SENSE                A7

// Define error code bits ------------------------------------------
#define BATT_ERR                  (1 << 0)   // battery low/bad voltage
#define TEMP_SENSE_ERR            (1 << 1)   // temp sensor not working
#define LED_DRV_ERR               (1 << 2)   // LED driver not working
#define CURRENT_SENSE_ERR         (1 << 3)   // current sensor not working
#define SERVO_POWER_ERR           (1 << 4)   // servo voltage not correct
#define FLASH_ERR                 (1 << 5)   // SPI flash error
#define RADIO_ERR                 (1 << 6)   // Radio error
#define SERVO_ERR                 (1 << 7)   // servo error (didn't move)


#endif

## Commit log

2025-01-14 v2.3 - Control board update
    - Added two P-channel MOSFETs in parallel for reverse protection of the battery to reduce RDS(ON)
    - Reduce MOSFETs gate pull-down resistor from 10k to 4.7k (account for increase in gate capacitance when using 2 FETs instead of 1)
    - Replace P-channel MOSFETS with SSM3J338R,LF - higher Id (6A) and lower RDS(ON) (17mohm)
    - INA219 is now powered from the 5V bus instead of 3.3V bus. This is to avoid potential issues in performance if 3.3V bus voltage drops down under 2.7V when servo is moving. All other sensors and ICs are fine down to 2V except INA219
    - Added logic level shifters for INA219 I2C bus to translate from 5V to 3.3V
    - Replaced the 3.3V power on all voltage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
2025-01-15 Added PNP file for v2.3 control board
2025-01-15 Added PNP file for v2.1 LED board
2025-03-09 v2.4 - Control board bug fixes
    - Remove extra 10K pull-ups on 3.3V I2C level shifter, since 4.7K I2C pull-ups already exist on the bus
    - Remove pull-up power circuitry. Now toggling directly from GPIO
    - Add NPN transistor to gate of Q2 to toggle display power properly
    - Add 10k bleed resistors to input and output of 5V boost regulator to drain the capacitors when power is turned off
    - Add layer numbers on each layer for reference
    - Made antenna trace curved
    - Add outline to ATMEGA1284P package (moved to tplace layer)
    - Add more vias to 5V line for better conductivity through traces
    - Change encoder MPN to PEC11R-4315F-S0012 (12 detents only)
    - Trace changes to accommodate new design
    - BOM, g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

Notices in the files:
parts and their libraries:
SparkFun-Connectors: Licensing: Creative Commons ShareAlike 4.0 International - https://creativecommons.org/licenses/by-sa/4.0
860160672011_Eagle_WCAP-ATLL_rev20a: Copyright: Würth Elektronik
